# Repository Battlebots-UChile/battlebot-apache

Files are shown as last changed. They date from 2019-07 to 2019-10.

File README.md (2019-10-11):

# Apache - 2019
Con su intimidante arma, Apache busca dejar inutilizable a los otros robots golpéandolos desenfrenadamente y a la vez no dejando que nadie se acerque. Siendo bastante liviano, el robot es capaz de maniobrar eficazmente pudiendo también hacer giros en el punto en que se encuentra.

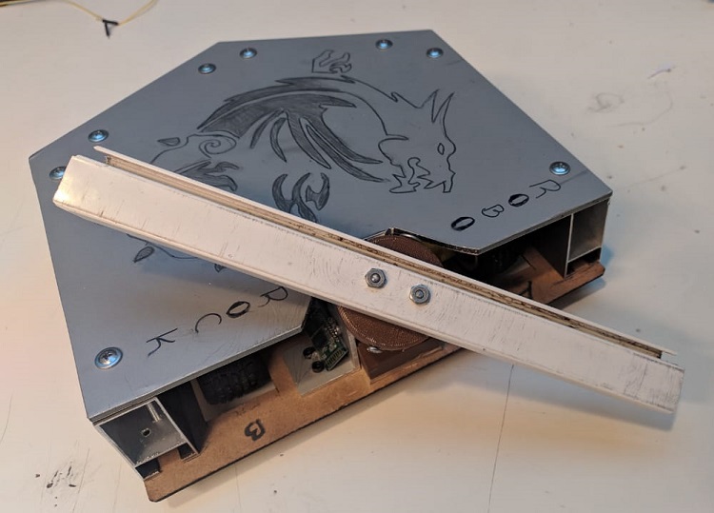
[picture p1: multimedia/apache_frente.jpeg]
Robot Apache


## Integrantes
- Hernán Cisternas - FCFM
- Isaias Venegas - FCFM
- Javier Ramirez - FCFM
- Matías Bustos - FCFM

## Descripción del proyecto
### Descripción morfológica
La forma recta de nuestro robot se inspiró en la base de una pirámide cuadrada, con un centro de gravedad muy bajo para no perder la estabilidad, mientras que el arma fue basada en las aspas de un helicóptero (de ahí viene el nombre Apache).  
Además en su parte trasera posee una forma puntiaguda, especial para la defensa recibiendo impactos.

### Estrategia utilizada
#### Ofensiva
Impactar la mayor cantidad de veces al robot enemigo usando la alta potencia del arma giratoria. 

#### Defensiva
Aprovechar la resistencia del material estructural y forma puntiaguda, recibiendo golpes en la parte trasera de Apache neutralizando momentaneamente la ofensiva del robot contrincante y empleando los distintos movimientos/giros implementados.

### Movimiento del robot (Aplicación Android)
**Para hacer uso de la aplicación es necesario emparejar previamente el módulo Bluetooth con un dispositivo con Sistema Operativo Android, luego se debe mantener activada la función Bluetooth del celular. Una vez hecho esto se debe presionar el botón "Conectar" situado en el extremo superior izquierdo de la App.**  
Buscando comodidad y facilidad de manejo la aplicación fue diseñada simulando un control de videojuegos, siendo el botón "A" para avanzar y el botón "B" para retroceder. Los botones con etiqueta "IZ" y "DER" realizan una curva dando una dirección, mientras que los botones "X" e "Y" permiten girar en el mismo sitio en sentido antihorario y horario respectivamente (útil para movimientos sorpresa tanto en ataque como defensa).  
Los botones restantes "QUE FOME", "IT'S OK", "A TODO GAS" y "ABORTEN" controlan el arma principal, ajustandola a velocidad mínima, media y máxima o parándolo en caso de ser necesario. Se recomienda utilizar las primeras dos velocidades.
Ante cualquier emergencia es posible desactivar a Apache apagando la función Bluetooth del dispositivo móvil.

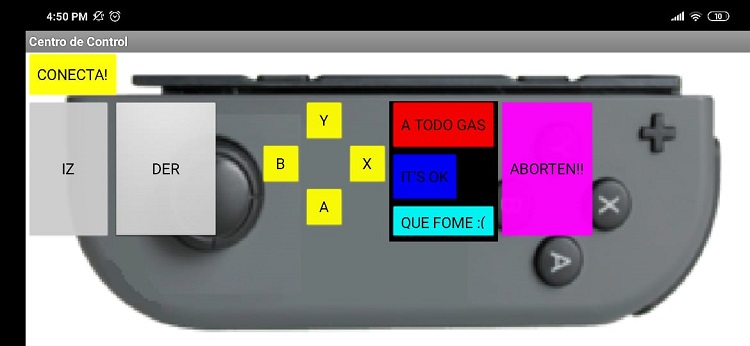
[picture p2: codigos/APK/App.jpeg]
App


### Diagrama funcional

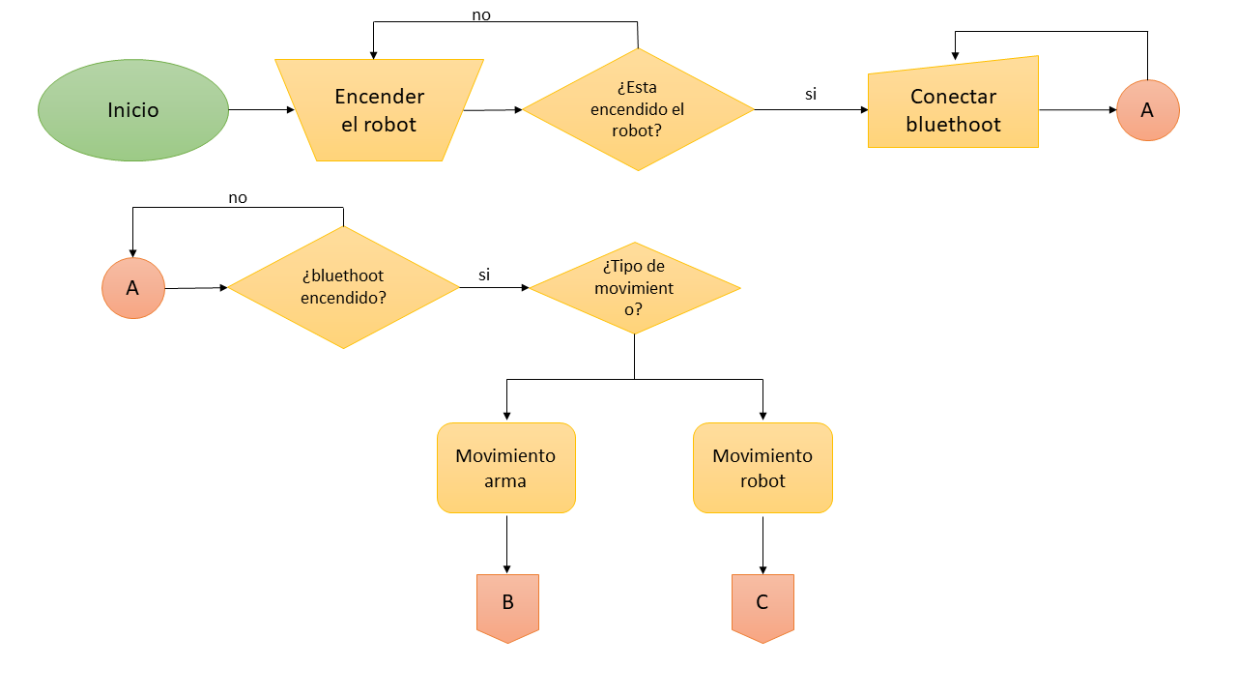
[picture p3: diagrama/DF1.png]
Diagrama 1

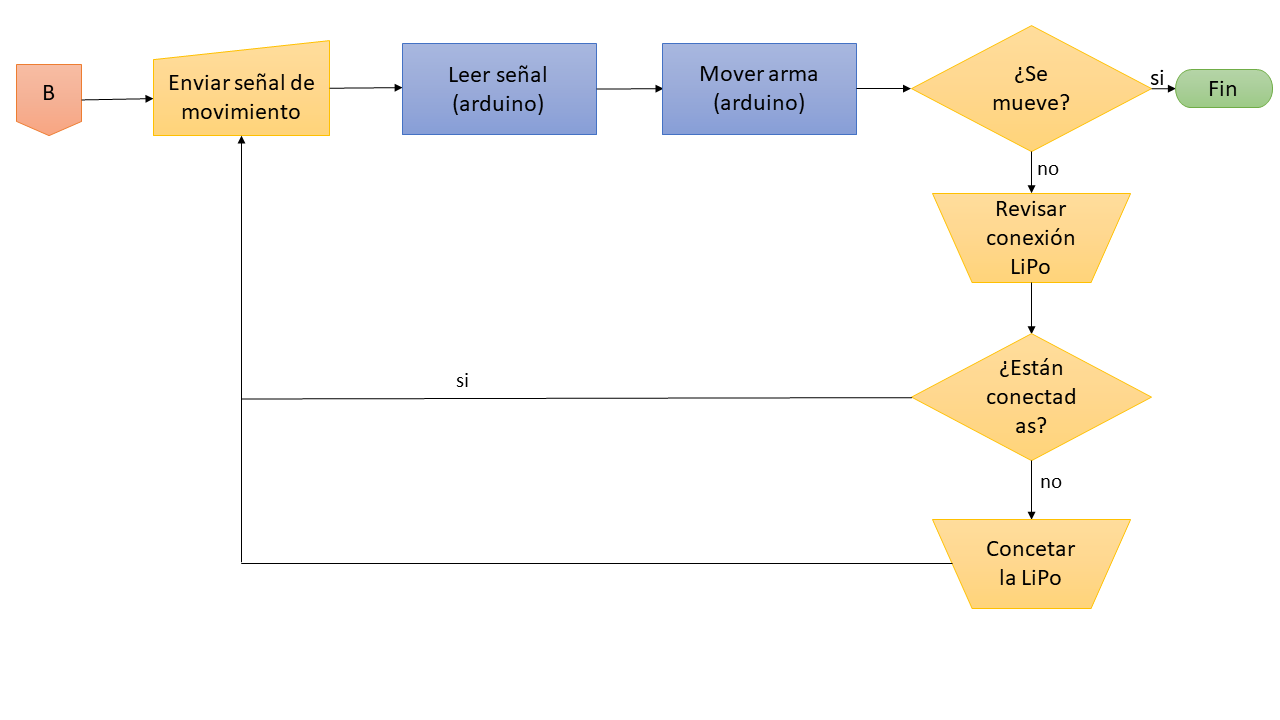
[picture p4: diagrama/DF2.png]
Diagrama 2

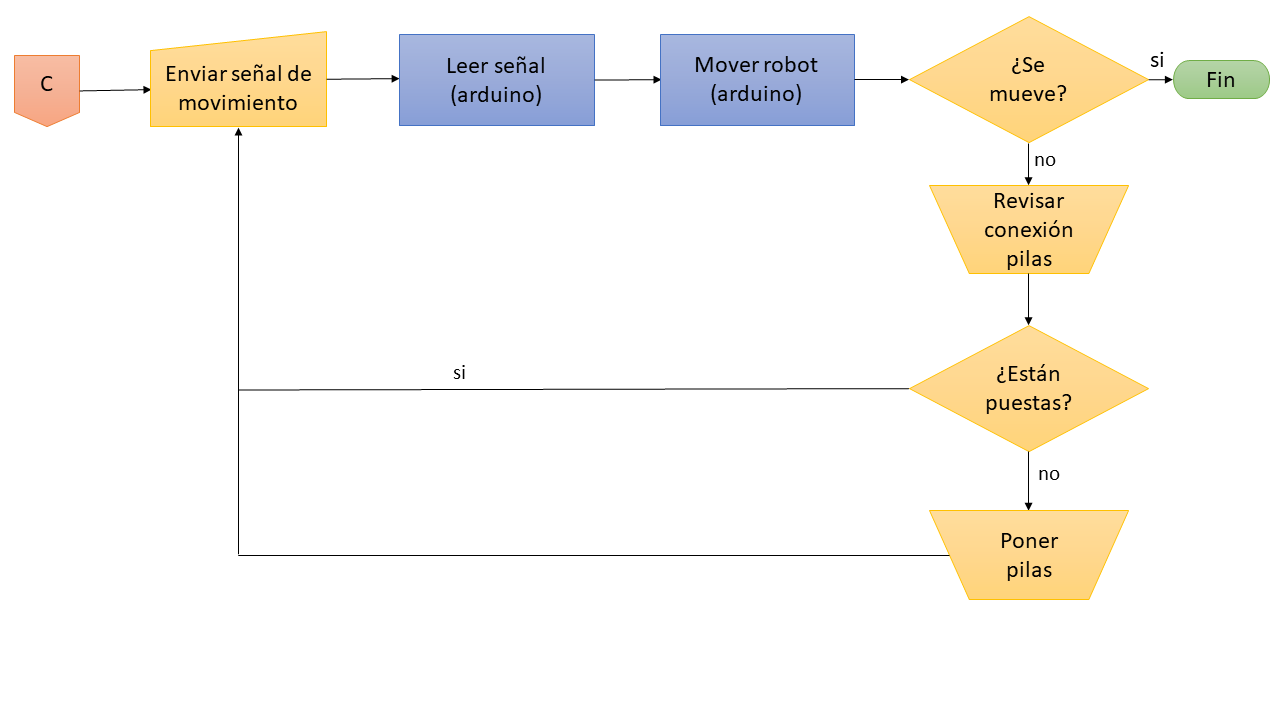
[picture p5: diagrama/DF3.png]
Diagrama 3


### Paso a Paso
#### Materiales y Herramientas
**Materiales**
1. Plancha de Madera tipo cartón o similar
2. Plancha de Alucobond
3. [Pieza circular](/planos/pieza%20circular.print) y [triangular](/planos/pieza%20triangular.print) en 3D
3. 2x Perfil de aluminio 
4. 4x Barra de aluminio (2 de 2,5x5x19cm y 2 de 11×1,5×5cm)
5. Barra de aluminio de 27×3×1,5cm (arma)
6. Placa Arduino UNO o compatible
7. 2x Rueda + Motor de 60mA y 3-6V
8. Rueda Loca
9. Módulo L298N Puente H con Jumper
10. Módulo HC-06 Bluetooth
11. Motor Dron Brushless A2212 1000kv + Controlador
12. Pilas que sumen 12V
13. Interruptor
14. Batería Li-Po Victory 11.1V 1300mah 15C 3 celdas
15. 8x Cable de largo 10-15cm
16. Soldadura
17. Pegamento industrial
18. Tornillos con tuerca
19. Portapilas
20. Cables Macho-Hembra Arduino
21. Alarma Li-Po (Opcional) 
22. Amarras plásticas (Opcional)
23. Protectores termoencogibles (tamaño según cables) / Silicona (Opcional)
  
**Herramientas**
1. Cortadora Láser / Sierra de mano (para cortar madera)
2. Impresora 3D
3. Sierra de mano (para cortar alucobond)
4. Taladro / Dremel (para agujeros en alucobond y aluminio)
5. Galletero (para cortar aluminio)
6. Alicate
7. APP
8. Lima (Opcional)
9. Lija (Opcional)

#### Construcción
**Recordatorio: Aunque la barra de aluminio no genera riesgo por si misma, al ser acoplada al motor de Dron resulta ser potencialmente peligrosa, por lo que es importante imprimir con alta densidad las piezas 3D (haciendolas más robustas), sujetar bien los componentes y guardar una debida distancia en todo momento**  

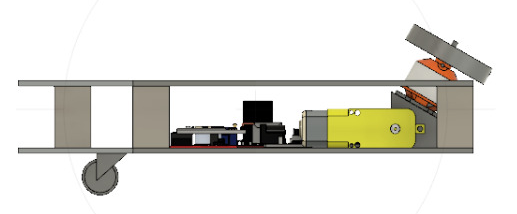
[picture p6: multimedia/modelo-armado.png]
modelo-armado
  
Nota: Se entenderá como el frente la parte donde se sitúa el arma. Se recomienda imprimir con tiempo las piezas 3D ya que el proceso es lento.
1. Cortar la base en madera según el [plano base](/planos/Plano_Base.pdf) usando una cortadora láser o dremel, junto con la [tapa](/planos/Plano_Tapa.pdf) en Alucobond usando las herramientas adecuadas.
2. Atornillar el motor de Dron a la pieza triangular impresa cuidando que el cable del controlador vaya hacia arriba y los tornillos superiores de la pieza sean los más cortos (esto dejará espacio para la placa Arduino). Poner tuercas correspondientes con la mayor fuerza posible.
3. Atornillar la pieza triangular impresa con la base de madera en el frente, luego sujetar con dos perfiles de aluminio (uno a cada lado).
4. Perforar dos agujeros en la barra de aluminio de 27x3x1,5cm siguiendo los [orificios de la pieza circular](/multimedia/pieza-circular.png) y hacer dos orificios simetricos a los lados en la pieza 3D (dónde irán un par de tornillos) junto con algunos cortes rectagulares en la base cilíndrica(evitará que el motor se caliente)
5. Con 2 tornillos [unir ambos](/multimedia/arma-ensamblada.jpeg) y fijar con las tuercas.
6. Unir a presión el arma con el motor de Dron encajando el orificio del centro de la pieza circular con el eje del motor. Apretarlo con tres tornillos (uno arriba con tuerca y dos a los lados). En caso de que el arma toque el suelo al girar, limar extremos.
7. Poner soldadura en los extremos de los cables.
8. Soldar un cable en cada polo de la placa de cada rueda y una vez seco cubrir con silicona o un protector termoencogible (esto aislará los extremos preveniendo un corte y quemar algún componente). 
9. Pegar las ruedas eléctricas encajándolas en los cortes hechos previamente (orientando su caja hacia adentro), luego sujetarlas con las amarras. 
10. Fijar con tornillos la Placa Arduino en la base de madera orientando la entrada de corriente hacia el frente del robot (facilita conectar los cables de los módulos al arduino).
11. [Poner un Jumper en el Puente H](https://youtu.be/c0L4gNKwjRw?t=70) en caso de no tenerlo (esto habilitará la entrada de 12V y salida de 5V). Fijar con tornillos el módulo en la base de madera, orientando la entrada de cables hacia abajo (lugar más amplio, facilitando la conexión con las ruedas).
12. Fijar con tornillos el portapilas. Las pilas se deben cubrir con una tapa de algun material sobrante y/o amarras plásticas.  
Retirando parcialmente los tornillos de los pines del puente H (atornillandolos tras cada instrucción), y siguiendo el [esquema](/diagrama/esquema_apache.jpg):
13. Conectar los cables de la rueda A: uno en Out1 y otro en Out2 del Puente H. Hacer lo mismo con los cables de la rueda B en Out3 y Out4.
14. Conectar desde el Puente H al Arduino:
- EN A -> Pin ~3
- IN 1 -> Pin 4
- IN 2 -> Pin 2
- EN B -> Pin ~11
- IN 3 -> Pin 7 
- IN 4 -> Pin 8
15. Dar energía a las ruedas:
- Positivo (+) de pilas -> Interruptor -> 12V (entrada izquierda del puente H).
- Negativo (-) de pilas -> GND (entrada central del puente H) y, con otro cable, 
    GND (puente H) -> GND (Arduino).
- 5V (Salida derecha del puente H) -> VIN (Arduino).
17. Dar energía al motor del arma:
- Positivo (+) del motor Dron -> Positivo (+) de batería Li-Po.
- Pin más cercano al Positivo del motor -> GND Arduino.
- Negativo (-) del motor Dron -> Negativo (-) de batería Li-Po.
- Pin más cercano al Negativo del motor -> Pin 10~
Se recomienda desenchufar luego de cada pelea debido a las características de las baterías Li-po (se vuelven inservibles si se llegan a descargar completamente. Para medir la energía restante se debe conectar una [alarma](https://youtu.be/6J3H2vQuFXY?t=118))
18. Conectar módulo Bluetooth a Arduino:
- VCC -> 5V
- GND -> GND
- TXD -> Pin 6~
- RXD -> Pin 5~
19. Colocar rueda "loca" centrada unos 4cm de la parte de atrás, teniendo cuidado con los cables.
20. Perforar las barras de 2,5x5x19cm por un lado para pasar los cables del motor de dron en una y el interruptor en la otra barra.
21. Fijar las barras de aluminio en los lados del robot sobre la plancha de madera.
22. Tapar con la pieza de alucobond y cortar una sección tal que el arma quede a la vista. Limar bordes y fijar con tornillos.
23. Descargar la aplicación, seguir las instrucciones de la sección "Movimiento del robot" y a pelear.

#### Problemas y soluciones
- P: Una rueda se mueve en un solo sentido. S: Prueba conectando los pines ENA/ENB en otros pines PMW ~, puede que estén dañados. Si no funciona, mueve las entradas del puente H.
- P: No se mueve una rueda. S: Es posible que el puente H tenga sus pines desgastados, prueba moviendo sus entradas o cambiando esos cables.
- P: No se mueve ninguna rueda. S: Quemaste el puente H suministrando 12V en la salida de 5V, consigue uno nuevo.
- P: Apesar de sólo querer avanzar, el robot se desvía a uno de los lados. S: Posiblemente las ruedas quedaron desalineadas por desgaste o al pegarlas mal, prueba avanzando en intervalos.
- P: Al golpear a otro robot Apache se desmayó. S: Las pilas quedaron sueltas, agrega más contención. Recomendamos *desactivar* el arma antes de golpear al contrincante, esto para no sobrecargar el motor y evitar el apagón.
- P: El arma se tambalea al hacerla girar. S: Los tornillos laterales no pesan lo mismo o la pieza circular se rompió; reemplázalos.

#### Proyecciones a futuro
- Mejorar la ventilación del motor de Dron rediseñando la pieza circular.
- Cubrir los componentes electrónicos del interior para protegerlos.
- Agregar sensores de tensión para que cuando el arma se detenga por golpear a otro robot, Apache pueda manejar la situación (girando en su eje dando un tiempo para que el arma vuelva a girar, por ejemplo).
- Probar con distintos materiales para la base, aumentando capas en caso de necesitar más peso (esto para evitar que con un ataque nuestro el robot salte).

## Licencia
<br />Esta obra está bajo una <a rel="license" href="http://creativecommons.org/licenses/by-nc/4.0/">Licencia Creative Commons Atribución-NoComercial 4.0 Internacional</a>.

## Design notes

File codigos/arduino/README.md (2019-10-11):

# Códigos Arduino

Código que permite **maniobrar** al robot según instrucciones enviadas desde la *aplicación Bluetooth*.

### Observaciones
- La libreria SoftwareSerial permite cambiar los pines de comunicación entre el Arduino y Bluetooth, evitando así quemar el módulo HC-06 y/o Arduino al transferir código a este último mientras se tiene el robot encendido. Los argumentos entregados son los nuevos pines para RXD y TXD del Arduino, siendo los inversos a los del módulo Bluetooth.
- La libreria Servo.h maneja la velocidad de giro del arma (SERVO.writeMicroseconds(vel_arma)). La velocidad mínima es de 1200, mientras que la máxima es de 2000 (ambas definidas por el fabricante del motor).
- El robot ejecutará la última acción que se le asigne desde la App del celular, diferenciando entre un mover ruedas momentaneamente y un cambio de velocidad en ataque. Es posible cambiar el carácter enviado, duración del movimiento, entre otros usando el programa AppInventor. Además es posible ver el estado/acción que realizará Apache desde la consola de Arduino mientras se tiene conectado al computador por cable USB.
- Gracias al puente H es posible asignar velocidades diferenciadas (de 0 a 255 usando analogWrite(enable_rueda,speed)) entre ambas ruedas, además de activar y desactivar un sentido de giro (usando digitalWrite(sentido_rueda,1))
    - Si se desea una trayectoria curva simulando ruedas direccionales, la rueda con menor velocidad será la que fije la dirección
    - Si se desea un giro en el mismo lugar, una rueda debe girar completamente en sentido horario mientras la otra lo hace de forma antihorario
    - Si se quiere un giro que describa un círculo, una rueda debe estar completamente quieta
- Tras diversas pruebas recomendamos disminuir la velocidad de giro de las ruedas para un mejor agarre de estas en superficies no porosas.

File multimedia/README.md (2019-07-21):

# Archivos multimedia de los battlebots

Se adjuntan:
- Fotos del armado
- Foto del proyecto terminado
- Vídeo de demostración/funcionamiento

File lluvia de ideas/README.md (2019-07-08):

# Lluvia de Ideas

Los bocetos que se encuentran aquí, son parte de la lluvia de ideas y posterior planificacion del robot, despues de una ardua comparación entre los posibles diseños, el ganador fue apache, el cual es una mezcla entre una cortadora de pasto y un helicoptero. 
Las mayores inspiraciones las encontramos en las batallas de robots profesionales y las fusionamos con nuestras ideas.

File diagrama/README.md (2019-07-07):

 # Diagrama electromecánico y de flujo

Esta carpeta contiene el diagrama electromecánico y el diagrama de flujo.

El diagrama electromecánico está hecho en Fritzing (contiene imagen y archivo .fzz)

Los archivos "DF1”,"DF2" y "DF3" corresponden a archivos .png en los cuales se muestran
un diagrama de flujo para el correcto funcionamiento del robot. Estos archivos deben ser
leídos en el orden anteriormente presentado para una compresión cabal de los mismos

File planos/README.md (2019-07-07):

# Archivos de planos incluidos

Subir al repositorio todos los modelos y planos utilizados para construir el battlebot:

- Modelo 3D
- Piezas 3D
- Planos de corte de cortadora láser (.pdf)

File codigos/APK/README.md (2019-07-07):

# Código de la Aplicación

Esta carpeta contiene todo lo necesario para el APK de Apache. 

Se puede utilizar directamente desde el archivo BattleBot2.apk o se puede importar usando el archivo BattleBot2.aia

Además, hay una imagen con los bloques de programación de AppInventor y la visual de la aplicación en el celular.

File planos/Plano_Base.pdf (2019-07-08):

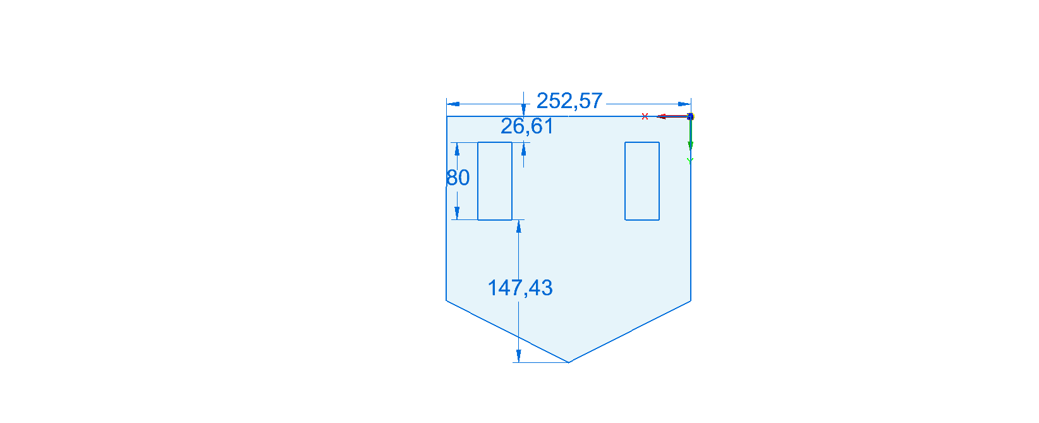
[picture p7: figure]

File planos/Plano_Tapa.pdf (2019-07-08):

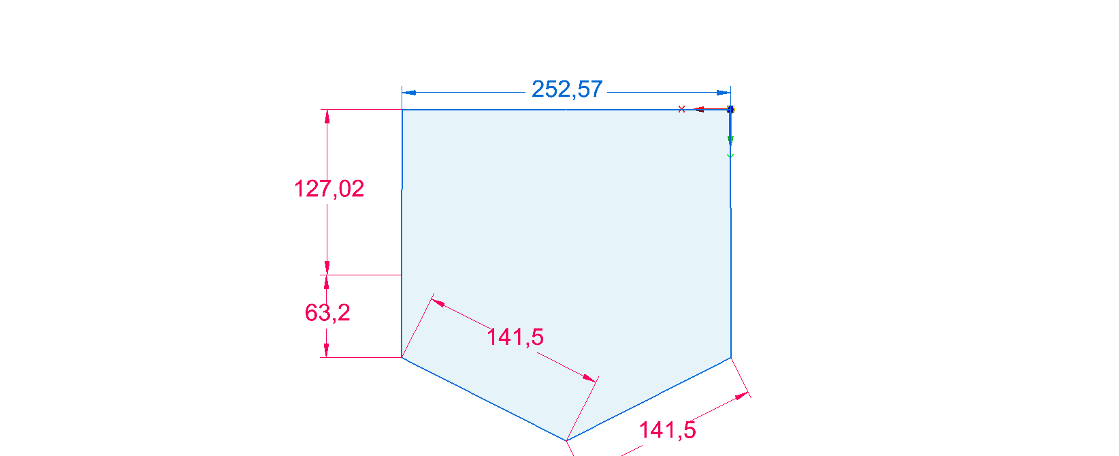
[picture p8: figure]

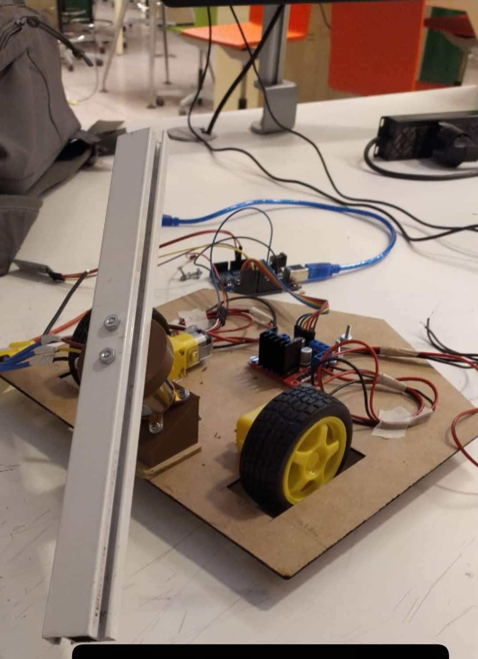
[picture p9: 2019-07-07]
multimedia/sin_proteccion.jpg

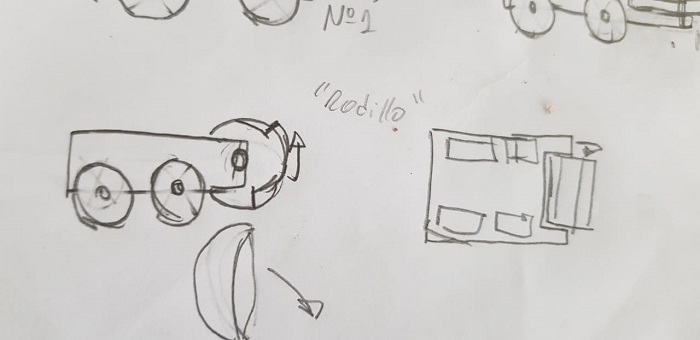
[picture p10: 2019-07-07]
lluvia de ideas/rodillo.jpeg

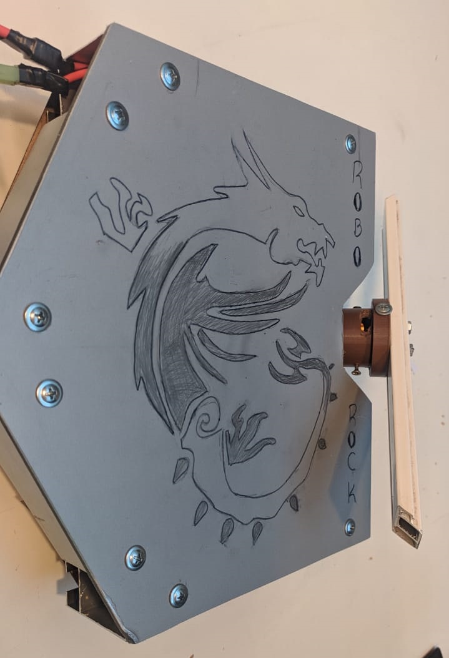
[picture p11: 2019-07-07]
multimedia/apache.jpeg

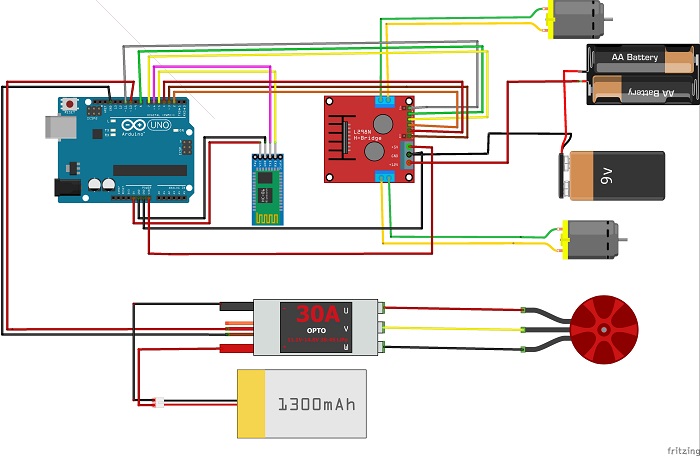
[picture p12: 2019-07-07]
diagrama/esquema_apache.jpg

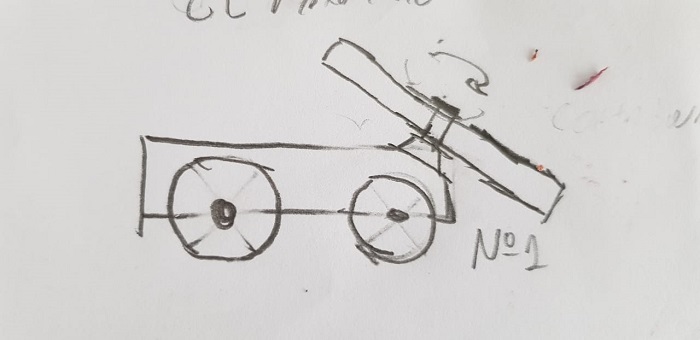
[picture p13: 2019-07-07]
lluvia de ideas/apache.jpeg

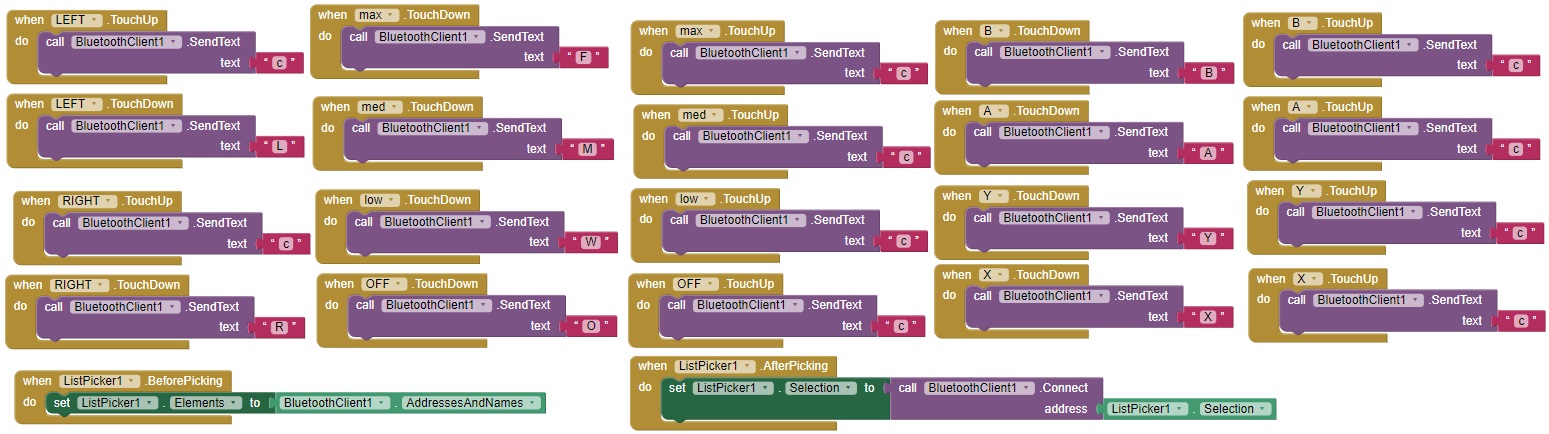
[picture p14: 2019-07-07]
codigos/APK/bloques_apk.jpg

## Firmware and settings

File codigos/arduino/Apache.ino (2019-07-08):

#include <SoftwareSerial.h>
#include<Servo.h>

// Definimos las variables
SoftwareSerial BT(6, 5); // TXD, RXD del Bluetooth
Servo ESC; // Crea un objeto de clase servo. Se trata del motor que activa el arma

int state; // El robot realizará la acción correspondiente al último estado
int speed = 255; // Velocidad de movimiento de las ruedas.
int arma = 1200; // Velocidad de ataque del arma.

// A: Rueda Izquierda
int en_A = 3; // Activa y potencia la rueda izquierda
int back_A = 4; // Variable que asigna un pin al movimiento antihorario de la rueda izquierda (retroceder)
int move_A = 2; // Variable que asigna un pin al movimiento horario de la rueda izquierda (avanzar)
// B: Rueda Derecha
int en_B = 11; // Activa y potencia la rueda derecha
int back_B = 8; // Variable que asigna un pin al movimiento horario de la rueda derecha (retroceder)
int move_B = 7; // Variable que asigna un pin al movimiento horario de la rueda derecha (retroceder)

void setup()
{
  ESC.attach(10); // Asigna un pin al motor del arma
  ESC.writeMicroseconds(1000); // Activa al motor del arma. 1000 = 1ms (el número depende del modelo del motor, pudiendo ser 1000 ó 2000)
  delay(5000); // Espera 5 segundos para activarse
  Serial.begin(9600); // Inicia la comunicación entre Arduino y PC
  BT.begin(9600); // Inicia la comunicación entre módulo HC-06 Bluetooth y APP
  Serial.setTimeout(10);
  // Inicializamos las variables
  pinMode(en_A, OUTPUT);
  pinMode(back_A, OUTPUT);
  pinMode(move_A, OUTPUT);
  pinMode(en_B, OUTPUT);
  pinMode(back_B, OUTPUT);
  pinMode(move_B, OUTPUT);
}

void loop()
{
  if (BT.available()>0) { // Si el módulo recibe señal enviada por la App
      state = BT.read(); // Leemos y guardamos el carácter recibido
  }
  if(state=='O'){ // Botón Aborten -> Apaga arma
      arma = 1200;
      ESC.writeMicroseconds(arma);
      Serial.println("Apaga ataque");
  }
  if(state=='F'){ // Boton Máxima Velocidad -> Giro del arma al máximo
      arma = 2000;
      ESC.writeMicroseconds(arma);
      Serial.println("Full ataque");
  }
  if(state=='M'){ // Boton Medio -> Giro del arma a nivel medio
      arma = 1500;
      ESC.writeMicroseconds(arma);
      Serial.println("Medio ataque");
  }
  if(state=='W'){ // Boton Mínimo -> Giro del arma a velocidad baja
      arma = 1300;
      ESC.writeMicroseconds(arma);
      Serial.println("Low ataque");
  }
  if(state=='c'){ // Sin Botón -> Parado (el arma sigue en funcionamiento en caso de estarlo)
      digitalWrite(move_A, 0);
      digitalWrite(back_A, 0);
      digitalWrite(move_B, 0);
      digitalWrite(back_B, 0);
      analogWrite(en_A, 0);
      analogWrite(en_B, 0);
  }
  if(state=='A'){ // Boton A -> Avanza
      digitalWrite(back_A, 0); // Se desactiva el sentido horario de la rueda izquierda
      digitalWrite(back_B, 0); // Se desactiva el sentido antihorario de la rueda derecha
      digitalWrite(move_A, 1); // Se activa el sentido antihorario de la rueda izquierda
      digitalWrite(move_B, 1); // Se activa el sentido horario de la rueda derecha
      analogWrite(en_A, speed); // Se imprime velocidad a la rueda izquierda
      analogWrite(en_B, speed); // Se imprime velocidad a la rueda derecha
      Serial.println("Avanza");
  }
  if(state=='B'){ // Boton B -> Retrocede
      digitalWrite(back_A, 1);
      digitalWrite(back_B, 1);
      digitalWrite(move_A, 0);
      digitalWrite(move_B, 0);
      analogWrite(en_A, speed);
      analogWrite(en_B, speed);
      Serial.println("Retrocede");
  }
  if(state=='L'){ // Cruceta Izquierda -> Trayectoria curva a la izquierda
      digitalWrite(back_A, 0);
      digitalWrite(move_A, 1);
      digitalWrite(back_B, 0);
      digitalWrite(move_B, 1);
      analogWrite(en_B, speed);
      analogWrite(en_A, 100); // Velocidad de la rueda izquierda menor a la rueda derecha
      Serial.println("Desplazamiento a la izquierda");
  }
  if(state=='R'){ // Cruceta Derecha -> Trayectoria curva a la derecha
      digitalWrite(back_B, 0);
      digitalWrite(move_B, 1);
      digitalWrite(back_A, 0);
      digitalWrite(move_A, 1);
      analogWrite(en_B, 100); // Velocidad de la rueda derecha menor a la rueda izquierda
      analogWrite(en_A, speed);
      Serial.println("Desplazamiento a la derecha");
  }
  if(state=='X'){ // Boton X -> Giro Derecha con centro interior
      digitalWrite(back_B, 1);
      digitalWrite(move_B, 0);
      digitalWrite(back_A, 0);
      digitalWrite(move_A, 1);
      analogWrite(en_B, speed);
      analogWrite(en_A, speed);
      Serial.println("Giro a la derecha");
  }
  if(state=='Y'){ // Boton Y -> Giro Izquierda con centro interior
      digitalWrite(back_B, 0);
      digitalWrite(move_B, 1);
      digitalWrite(back_A, 1);
      digitalWrite(move_A, 0);
      analogWrite(en_B, speed);
      analogWrite(en_A, speed);
      Serial.println("Giro a la derecha");
  }
} 

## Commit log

2019-06-16 Se incluye codigo Arduino
2019-06-17 Se elimina esquema de ejemplo y se agrega el esquema de apache
2019-06-17 se agrega el diagrama electro-mecánico de apache
2019-07-07 Se actualiza la informacion del robot, incluyendo integrantes del proyecto, estrategias, movimiento y construccion paso a paso. Cambio minusculo en el archivo README del codigo arduino
2019-07-07 cambio en tamañp de esquema
2019-07-07 Cambios en README y se añadieron los archivos .print de 'pieza circular' y 'pieza traingular'
2019-07-07 cambio en tamaño de esquema
2019-07-07 Se modifica tamaño en esquema de apache y se agrega arcchivo fritzing
    [apache.fzz]
2019-07-07 Se agrega imagenes de la lluvia de ideas
2019-07-07 Se agrega imagen de bloques del apk
2019-07-07 mejor escalado de bloque de apk
2019-07-07 Se agrega foto de robot apache
2019-07-07 se agrega foto de apache de frente
2019-07-07 Se cambia foto de apache, por una de frente
2019-07-07 Se comenta que contiene esta carpeta
2019-07-07 Se agrega foto de como se ve la aplicación desde un celular
2019-07-07 mas bonito el readme
2019-07-07 se comenta el README
2019-07-07 se agrega video de funcionamiento del arma
2019-07-07 se agrega foto de apache sin su proteccion
2019-07-07 Cambios en README 'Diagramas de flujo'
2019-07-08 Se agregaron archivos .par y .pdf de la base y de la tapa
2019-07-08 breve descripción de las ideas
2019-07-08 Se actualiza informacion de Apache. Se separa codigo Arduino del Readme y se actualiza
2019-07-10 Se agregan videos de momentos en que el arma se rompe
2019-07-10 Se actualiza información acerca de un material para la construccion (Cables Arduino pasa de Opcional a Necesario)
2019-07-10 Se agrega un espacio de linea en una instruccion
2019-07-12 Se mejora la redacción en Paso a Paso
2019-10-11 Se agrega una respuesta en la sección FAQ
